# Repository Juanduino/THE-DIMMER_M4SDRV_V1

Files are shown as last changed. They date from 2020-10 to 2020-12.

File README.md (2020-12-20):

# THE DIMMER_M4SDRV_V1
Linear BLDC motor controller with TMC2209 for rotation dev. based on SAMD(E)51 MCU. The primary goal of this project is to make a linear motor controller, which can control the (single or multiple) Z axis and rotation on openPnP machines. With that said, the hardware could be used to control other (sub 10amp) 3 phase motors or steppers. In the openPnP community, there has been development on multi-nozzle machines for some time. This is an attempt to simplify and specify the hardware for openPnP machines.

By introducing sub-controllers in openPnP, it is now possible to delegate various tasks to various controllers. This project builds on that feature. Each z-axis subcontroller, will connect to the mainframe by either USB or CAN

Files are made with Kicad Nightly Build. If you have the latest stable releace installed, you can install the Nightly build next to it in eg. KicadNightly folder. Just dont install systam variables, which is chosen in the install guide.

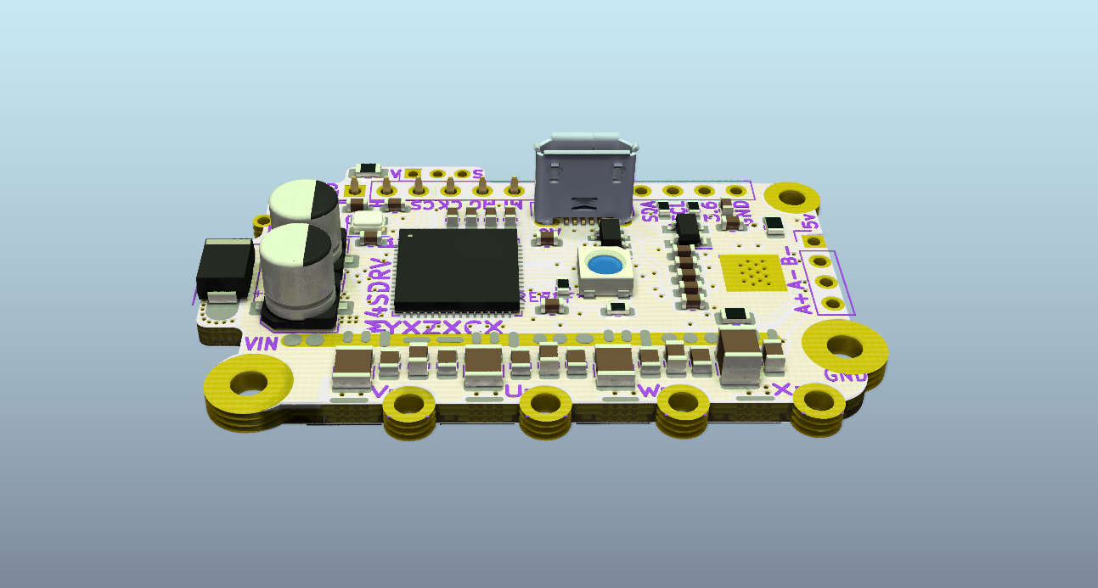
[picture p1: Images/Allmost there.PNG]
TOP


PROS: 

By using a linear 3 phase motor controller with an onboard stepper IC for rotation, wires can be kept very short.
 
The linear motor is easy to make yourself with common 3mm long neodymium magnets. (Onboard Hall sensors is spaced apart, with the appropriate distance for these magnets). Likewise a external (angle)sensor can be connected via SPI, I2C or Serial.
 
To make the motor, the idea is to fill up a eg. stainless steel pipe with magnets and spacers between those magnets. The coils of the motor will be wound on a 3D printed "slider" (bushing) with the appropriate spacing to match the magnet's length (3mm).
 
By winding the coils around the magnets, the entire pull/push of the magnets is used and the linear motor is not as sensitive to the distance between coils and magnets.
 
The south and north pole of the coils will be in the direction of movement, unlike normal BLDC motors, where you make two windings for each pole pair.
 
Mosfets have quite different specs. when it comes to voltages and current ratings. If using 12v or 24v for a motor, its better to use 30v rated mosfets with a much lower Rds(on) (resistence) compared to higher voltage rated MOSFETS. 
The amount of heat dissipated from the Mosfets can be calculated. (see page 3 https://d1d2qsbl8m0m72.cloudfront.net/en/products/databook/applinote/ic/power/switching_regulator/power_loss_appli-e.pdf)

CONS: It takes time to perfect. All good cookies take time to make. The intended Arduino Library (SimpleFoc) needs further development to be able to work with inline current sensing.

Changelog:

Added BusBar footprint for 1.5mm copper wire. This add´s some 50amp rating to the VIN line. (@10C rise)

Mosfets are rated for MAX 60amp pulsed current.

Added MAX40056 Current sensor on 3 out of 4 phases. The last fase will have to follow one of the ones with sensor if used seperately. In stepper configuration, the sensor will monitor the two windings on two bidirectional sensors.
In 3 phase configuration, the 3 current sensors will be in use. The MAX40056 has advanced PWM rejection, and ultra fast settle time. This ensures a good read in harsh PWM invironments.

Added MOSFET driver MIC4605-2 which control high side & Low side using one PWM input. This mean we can use the SimpelFOC lib. as is (Current sense still need implementation).
This driver is not just fast its totally fast. Combined with the ultra low Gate charge and rise/fall time of the Infinion Mosfets, hopefully this will keep things cool.
 
Note: Adafruit is adding support for SAME51, which has native CAN FD support.
(source: https://github.com/adafruit/ArduinoCore-samd/pull/267)

HARDWARE:

SAME51 MCU 120 mhz M4 architecture with CAN FD (https://www.microchip.com/wwwproducts/en/ATSAME51J20A)

TMC2209 stepper driver (https://www.trinamic.com/products/integrated-circuits/details/tmc2209-la/)

MOSFETS BSC0925ND Dual channal 40amp 17nC gate charge (https://www.infineon.com/cms/en/product/power/mosfet/12v-300v-n-channel-power-mosfet/bsc0925nd/)

Gate drivers MIC4605-2 PWM indput (https://www.microchip.com/wwwproducts/en/MIC4605)

Current sensors MAX40056 (https://datasheets.maximintegrated.com/en/ds/MAX40056F-MAX40056U.pdf)

Step-Down converter 4v/36v to 10v rail 1amp (https://www.ti.com/product/LMR50410)

3.6v LDO 500mA (https://ww1.microchip.com/downloads/en/DeviceDoc/MIC5219-500mA-Peak-Output-LDO-Regulator-DS20006021A.pdf)

3 x ANALOG HALL sensors (https://www.ti.com/product/DRV5053?qgpn=drv5053)

Analog hall sensors will potentially give a precision of the ADC resolution over one polepair. Thats 12bit (4096:1) (3mm/4096=0,0007mm)

CAN FD physical layer IC MCP2562FD-E_SN 8Mbps (https://www.microchip.com/wwwproducts/en/MCP2562FD)

4 layer PCB w. 105µm outer copper. (Min 0.25 mm. trace width and clearence)

Communication ports:

SERCOM port can be configuered to I2C, SPI and serial.

CAN FD is integrated into the SAME51 MCU.

USB 2.0 full speed. (USB port data-pins is broken out)

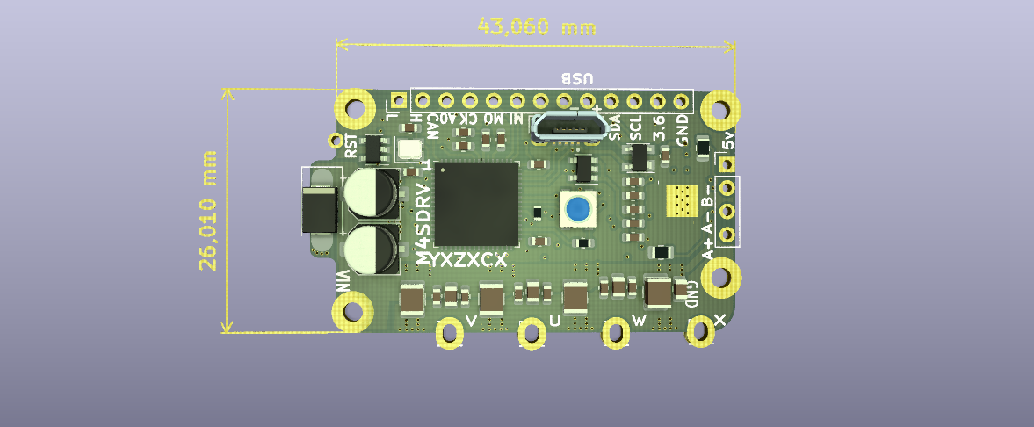
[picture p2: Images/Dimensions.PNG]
Dimensions


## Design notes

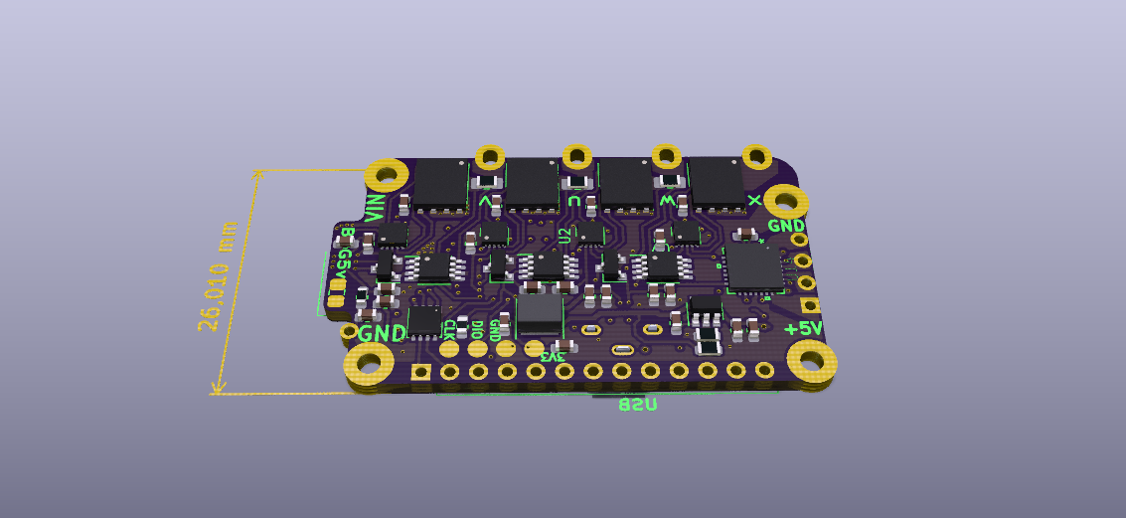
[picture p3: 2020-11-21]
Images/FLIPSIDE.PNG

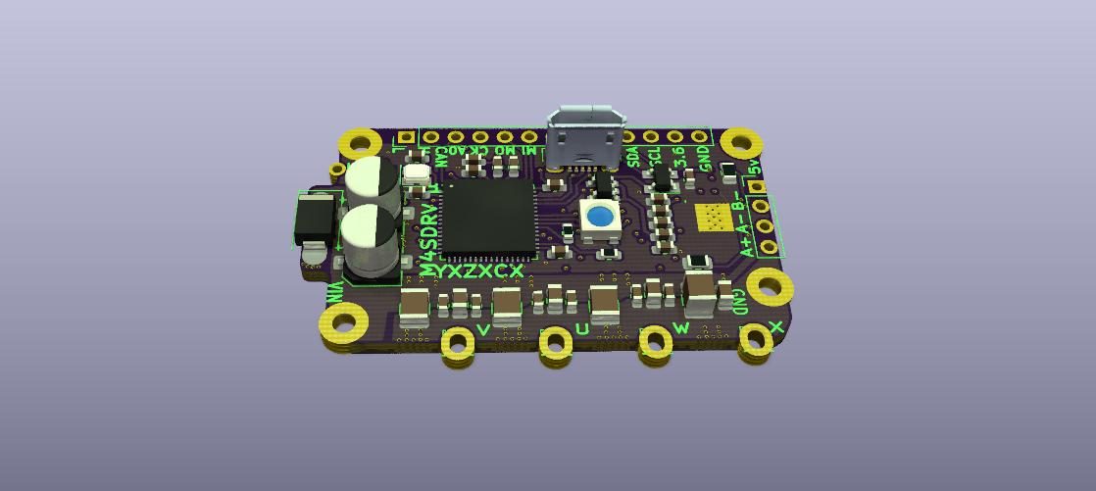
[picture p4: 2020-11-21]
Images/TOP.PNG

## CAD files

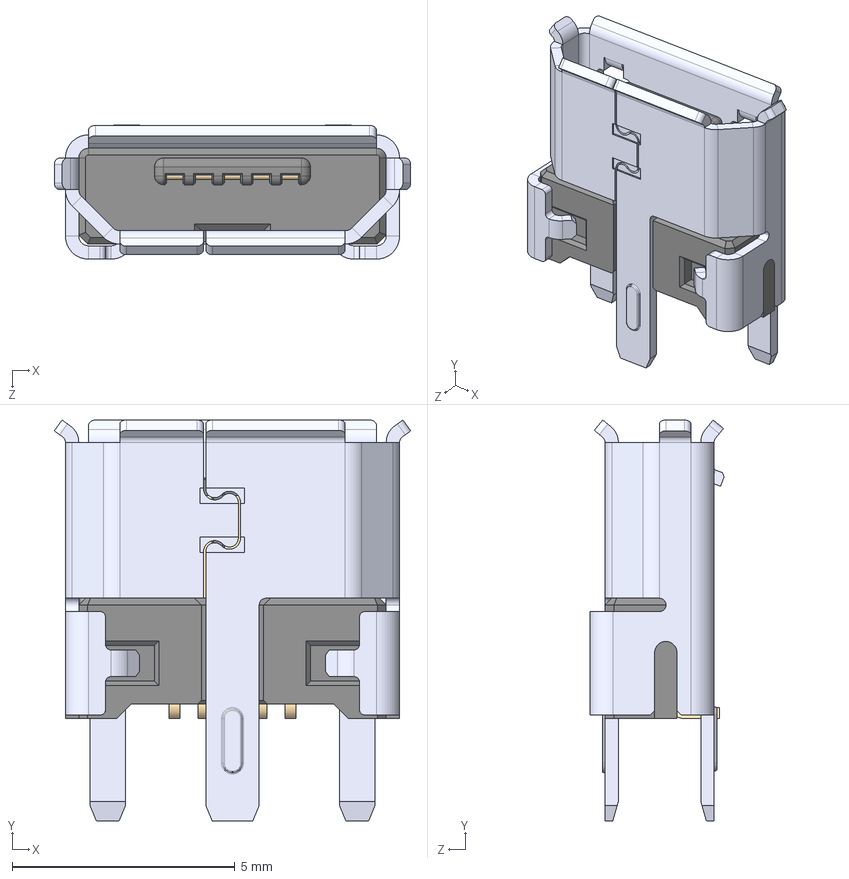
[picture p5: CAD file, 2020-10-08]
3dmodels/molex_USB_vert.STEP
8.00 x 9.00 x 3.01 mm

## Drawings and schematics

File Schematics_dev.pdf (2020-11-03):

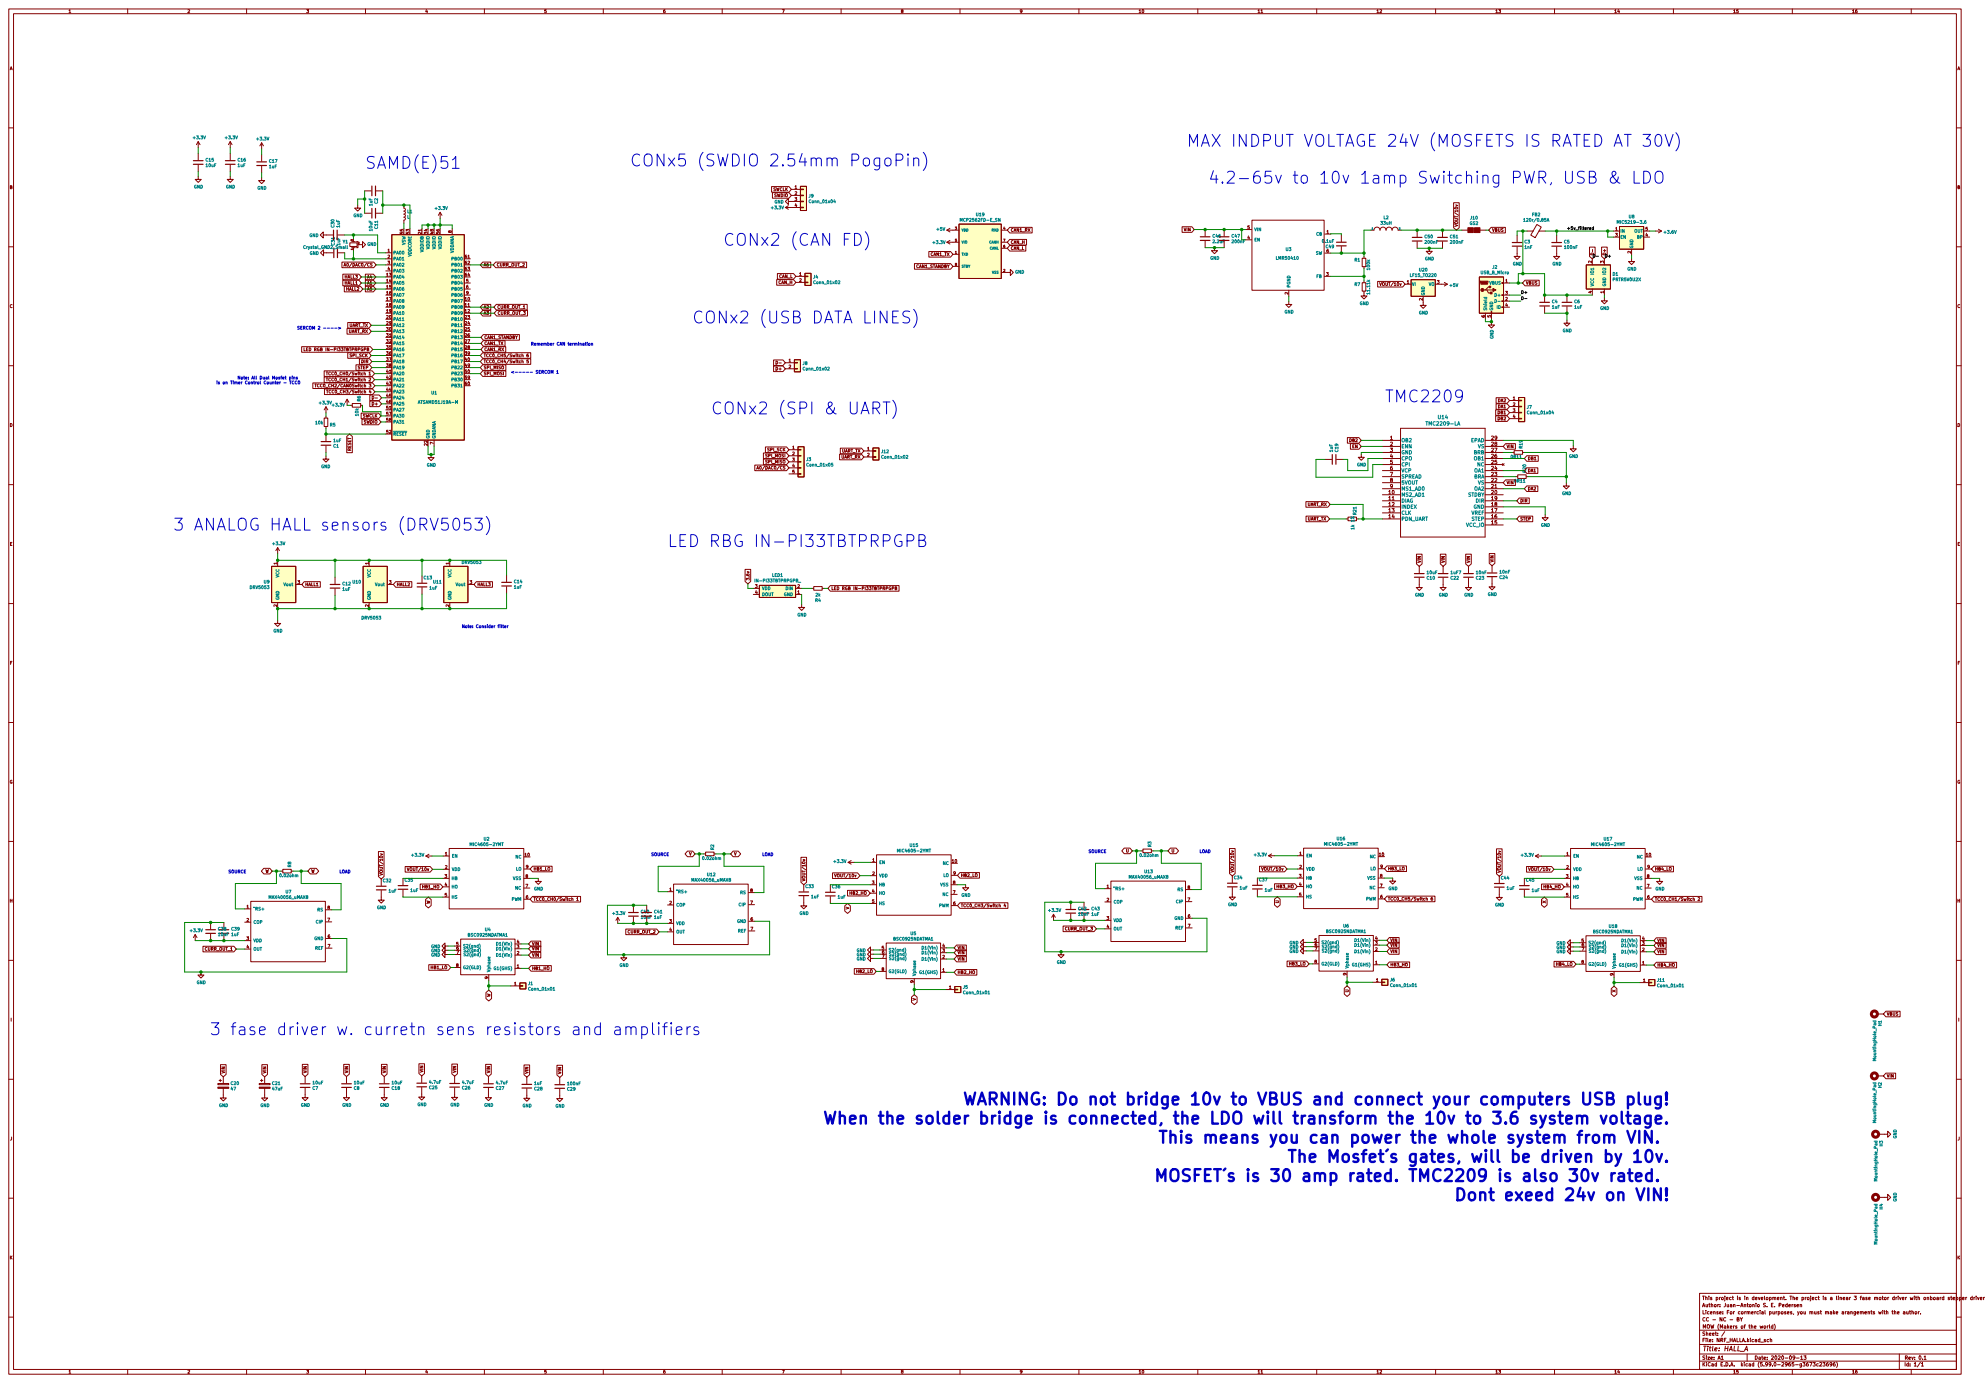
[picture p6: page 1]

SERCOM 2 ----> Note: All Dual Mosfet pins

SOURCE WARNING: Do not bridge 10v to VBUS and connect your computers USB plug!

9 U5 BSC0925NDATMA1 GND GND GND GND

VBUS VIN
3 fase driver w. curretn sens resistors and amplifiers

When the solder bridge is connected, the LDO will transform the 10v to 3.6 system voltage.

This means you can power the whole system from VIN.

Dont exeed 24v on VIN!

License: For cormercial purposes, you must make arangements with the author. Author: Juan-Antonio S. E. Pedersen This project is in development. The project is a linear 3 fase motor driver with onboard stepper driver for rotation.

File: NRF_HALLA.kicad_sch Sheet: / MOW (Makers of the world) CC - NC - BY

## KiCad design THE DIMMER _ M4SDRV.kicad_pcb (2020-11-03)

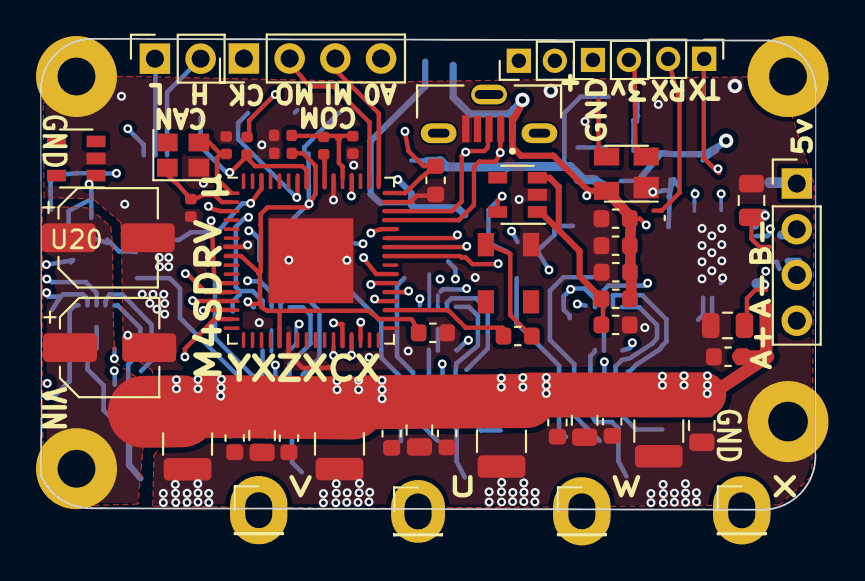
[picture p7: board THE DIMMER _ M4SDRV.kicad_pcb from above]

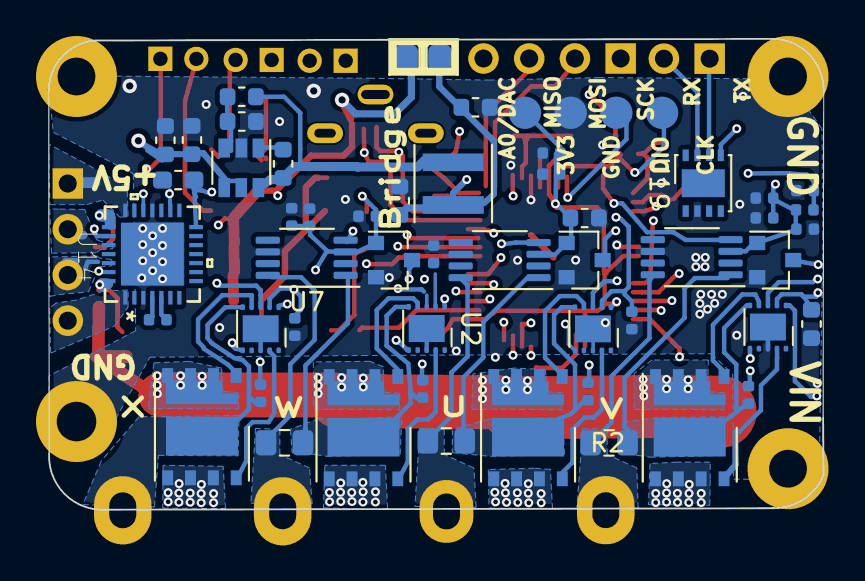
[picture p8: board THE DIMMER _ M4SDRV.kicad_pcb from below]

Board: 4 copper layers, 43.1 x 26.2 mm, 106 parts (51 on the bottom side), 68 nets.

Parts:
C1, C2, C12, C13, C16, C19, C30, C31, C33, C34, C35, C36, C37, C39, C41, C43, C44, C45: 1uF; C_0402_1005Metric
C3: 1nF; C_0603_1608Metric
C4, C6, C14, C17, C28, C28#2, C32: 1uF; C_0603_1608Metric
C5, C29: 100nF; C_0603_1608Metric
C7, C8, C10, C18: 10uF; C_1210_3225Metric
C11: 10uF; C_0402_1005Metric
C15: 10uF; C_0603_1608Metric
C20: 47; CP_Elec_5x5.8
C21: 47uF; CP_Elec_5x5.8
C22, C22#2: 1uF7; C_0603_1608Metric
C23, C24: 10nF; C_0603_1608Metric
C25, C25#2, C26, C27: 4.7uF; C_0805_2012Metric
C38, C40, C42: 10nF; C_0402_1005Metric
C46: 2.2uF; C_0603_1608Metric
C47, C50, C51: 200nF; C_0603_1608Metric
C49: 0.1uF; C_0603_1608Metric
D1: PRTR5V0U2X; SOT-143
FB2: 120r/0.85A; C_0603_1608Metric
H1, H2, H3, H4: MountingHole_Pad; MountingHole_2.2mm_M2_ISO14580_Pad_TopBottom
J1, J5, J6, J11: Conn_01x01; PinHeader_1x01_P2.54mm_Vertical
J2: USB_B_Micro; MOLEX_1051330001
J3: Conn_01x05; PinHeader_1x04_P2.54mm_Vertical
J4: Conn_01x02; PinSocket_1x02_P2.54mm_Vertical
J7: Conn_01x04; PinHeader_1x04_P2.54mm_Vertical
J8, J8#2, J12: Conn_01x02; PinHeader_1x02_P2.00mm_Vertical
J9: Conn_01x04; POGO
J10: GS2; R_0805_2012Metric
L1: L; L_0402_1005Metric
L2: 33uH; L_Coilcraft_XxL4020
LED1: IN-PI33TBTPRPGPB_; IN-PI33TBTPRPGPB
R1: 100k; R_0603_1608Metric
R2, R3, R8: 0.02ohm; R_0805_2012Metric_Pad1.15x1.40mm_HandSolder
R4: 2k; R_0603_1608Metric
R5, R6: 10k; R_0402_1005Metric
R7: 11.11k; R_0603_1608Metric
R19, R20: 0R11; R_0805_2012Metric
R21: 1k 1%; R_0603_1608Metric_Pad1.05x0.95mm_HandSolder
U1: ATSAMD51J19A-M; QFN-64-1EP_9x9mm_P0.5mm_EP4.7x4.7mm
U2, U15, U16, U17: MIC4605-2YMT; MIC4605
U3: LMR50410; SOT-23-6
U4, U5, U6, U18: BSC0925NDATMA1; Infineon_PG-TISON-8-2
U7, U12, U13: MAX40056_uMAX8; MAX40056F
U8: MIC5219-3.6; SOT-23-5
U9, U10, U11: DRV5053; SOT-23
U14: TMC2209-LA
U19: MCP2562FD-E_SN; DFN-8-1EP_3x3mm_P0.65mm_EP1.55x2.4mm
U20: LF15_TO220; SOT-23-5
Y1: Crystal_GND2_Small; Crystal_SMD_2520-4Pin_2.5x2.0mm

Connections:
+3V3: C12.1, C13.1, C14.1, C15.1, C16.1, C17.1, C38.2, C39.2, C40.2, C41.2, C42.2, C43.2, J9.4, R5.2, R6.2, U1.8 (VDDANA), U1.21 (VDDIOB), U1.34 (VDDIO), U1.48 (VDDIO), U1.56 (VDDIO), U2.1 (EN), U7.3 (VDD), U8.5 (OUT), U9.1 (VCC), U10.1 (VCC), U11.1 (VCC), U12.3 (VDD), U13.3 (VDD), U15.1 (EN), U16.1 (EN), U17.1 (EN), U19.5 (VIO)
+5V: U19.3 (VDD), U20.3 (VO)
/+5v_filtered: C5.1, FB2.2, U8.1 (IN), U8.3 (EN)
A0/DAC0/CS: J3.4, U1.3 (PA02)
A1: U1.14 (PA05), U9.3 (Vout)
A2: U1.11 (PB08), U7.4 (OUT)
A3: U1.12 (PB09), U13.4 (OUT)
A4: U1.13 (PA04), U11.3 (Vout)
A5: U1.15 (PA06), U10.3 (Vout)
A6: U1.62 (PB01), U12.4 (OUT)
CAN1_RX: U1.28 (PB15), U19.4 (RXD)
CAN1_STANDBY: U1.26 (PB13), U19.8 (STBY)
CAN1_TX: U1.27 (PB14), U19.1 (TXD)
CAN_H: J4.2, U19.7 (CANH)
CAN_L: J4.1, U19.6 (CANL)
D+: D1.3 (IO2), J2.3 (D+), J8.2, J8#2.2, U1.46 (PA25)
D-: D1.2 (IO1), J2.2 (D-), J8.1, J8#2.1, U1.45 (PA24)
DA1: J7.2, U14.24 (OA1)
DA2: J7.1, U14.21 (OA2)
DB1: J7.3, U14.26 (OB1)
DB2: J7.4, U14.1 (OB2)
DIR: U1.37 (PA18), U14.19 (DIR)
GND: C1.1, C2.2, C3.2, C4.2, C5.2, C6.2, C7.1, C8.1, C10.1, C11.2, C12.2, C13.2, C14.2, C15.2, C16.2, C17.2, C18.1, C20.2, C21.2, C22.1, C22#2.1, C23.1, C24.1, C25.1, C25#2.1, C26.1, C27.1, C28.1, C28#2.1, C29.1, C30.1, C31.1, C32.2, C33.2, C34.2, C38.1, C39.1, C40.1, C41.1, C42.1, C43.1, C44.2, C46.2, C47.2, C50.2, C51.2, D1.1 (GND), H3.1, H4.1, J2.5 (GND), J9.3, LED1.1 (GND), R7.2, R19.1, R20.1, U1.7 (GNDANA), U1.22 (GND), U1.33 (GND), U1.47 (GND), U1.54 (GND), U1.65 (GND), U2.8 (VSS), U3.2 (PGND), U4.5 (S2(gnd)), U4.6 (S2(gnd)), U4.7 (S2(gnd)), U5.5 (S2(gnd)), U5.6 (S2(gnd)), U5.7 (S2(gnd)), U6.5 (S2(gnd)), U6.6 (S2(gnd)), U6.7 (S2(gnd)), U7.6 (GND), U8.2 (GND), U9.2 (GND), U10.2 (GND), U11.2 (GND), U12.6 (GND), U13.6 (GND), U14.3 (GND), U14.18 (GND), U14.29 (EPAD), U15.8 (VSS), U16.8 (VSS), U17.8 (VSS), U18.5 (S2(gnd)), U18.6 (S2(gnd)), U18.7 (S2(gnd)), U19.2 (VSS), U20.2 (GND), Y1.2
HB1_HO: U2.4 (HO), U4.1 (G1(GHS))
HB1_LO: U2.9 (LO), U4.8 (G2(GLD))
HB2_HO: U5.1 (G1(GHS)), U15.4 (HO)
HB2_LO: U5.8 (G2(GLD)), U15.9 (LO)
HB3_HO: U6.1 (G1(GHS)), U16.4 (HO)
HB3_LO: U6.8 (G2(GLD)), U16.9 (LO)
HB4_HO: U17.4 (HO), U18.1 (G1(GHS))
HB4_LO: U17.9 (LO), U18.8 (G2(GLD))
LED RGB IN-PI33TBTPRPGPB: R4.1, U1.35 (PA16)
unnamed: C2.1, C11.1, L1.1, U1.53 (VDDCORE)
unnamed: C19.1, U14.4 (CPO)
unnamed: C19.2, U14.5 (CPI)
unnamed: C30.2, U1.1 (PA00), Y1.3
unnamed: C31.2, U1.2 (PA01), Y1.1
unnamed: C35.1, U2.3 (HB)
unnamed: C36.1, U15.3 (HB)
unnamed: C37.1, U16.3 (HB)
unnamed: C45.1, U17.3 (HB)
unnamed: C49.1, L2.1, R1.1, U3.6 (SW)
unnamed: C49.2, U3.1 (CB)
unnamed: L1.2, U1.55 (VSW)
unnamed: LED1.2 (DIN), R4.2
unnamed: R1.2, R7.1, U3.3 (FB)
unnamed: R19.2, U14.27 (BRB)
unnamed: R20.2, U14.23 (BRA)
RESET: C1.2, R5.1, U1.52 (~RESET)
SPI_MISO: J3.3, U1.49 (PB22)
SPI_MOSI: J3.2, U1.50 (PB23)
SPI_SCK: J3.1, U1.36 (PA17)
STEP: U1.38 (PA19), U14.16 (STEP)
SWCLK: J9.1, R6.1, U1.57 (PA30)
SWDIO: J9.2, U1.58 (PA31)
TCC0_CH0/Switch 1: U1.41 (PA20), U2.6 (PWM)
TCC0_CH1/Switch 2: U1.42 (PA21), U17.6 (PWM)
TCC0_CH3/Switch 4: U1.44 (PA23), U15.6 (PWM)
TCC0_CH5/Switch 6: U1.39 (PB16), U16.6 (PWM)
U: C37.2, J6.1, R3.1, R3.2, U6.9 (Vphase), U13.1 (¨RS+), U13.8 (RS), U16.5 (HS)
UART_RX: J12.2, R21.1, U1.30 (PA13), U14.14 (PDN_UART)
UART_TX: J12.1, R21.2, U1.29 (PA12)
V: C36.2, J5.1, R2.1, R2.2, U5.9 (Vphase), U12.1 (¨RS+), U12.8 (RS), U15.5 (HS)
VBUS: C3.1, C4.1, C6.1, D1.4 (VCC), FB2.1, H1.1, J2.1 (VBUS), J10.2 (G2)
VIN: C7.2, C8.2, C10.2, C18.2, C20.1, C21.1, C22.2, C22#2.2, C23.2, C24.2, C25.2, C25#2.2, C26.2, C27.2, C28.2, C28#2.2, C29.2, C46.1, C47.1, H2.1, U3.4 (EN), U3.5 (VIN), U4.2 (D1(Vin)), U5.2 (D1(Vin)), U6.2 (D1(Vin)), U14.22 (VS), U14.28 (VS), U18.2 (D1(Vin))
VOUT/10v: C32.1, C33.1, C34.1, C44.1, C50.1, C51.1, J10.1 (G1), L2.2, U2.2 (VDD), U15.2 (VDD), U16.2 (VDD), U17.2 (VDD), U20.1 (VI)
W: C35.2, J1.1, R8.1, R8.2, U2.5 (HS), U4.9 (Vphase), U7.1 (¨RS+), U7.8 (RS)
X: C45.2, J11.1, U17.5 (HS), U18.9 (Vphase)

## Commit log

2020-10-06 Added curretn sensor and driver
    Added current sensor MAX40056 and MOSFET driver MIC4605-2YMT.
    [THE DIMMER _ M4SDRV.kicad_pcb, THE DIMMER _ M4SDRV.kicad_sch]
2020-10-07 Added 4th Bridge
    This adds support for controlling steppers using SimpelFOC lib. Yes with 40 amp rated bridges. Added current sensors, which will be sensitive in the low regions.
2020-10-07 Create ADD_driver and current sensor.PNG
    TOP side
2020-10-08 Better to have USB facing out, if the boards are mounted on a pnp head
2020-10-09 added switching regulator for 10v gate rail
2020-11-17 Update Dimensions.PNG
    Almost there. Added a few millimeters to make room for the CAN FD tranciever and USB data lines. The dimensions is still way within the NEMA17 width, which should give access to the NEMA17 assembly b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

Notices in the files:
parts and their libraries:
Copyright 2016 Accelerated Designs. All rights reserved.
